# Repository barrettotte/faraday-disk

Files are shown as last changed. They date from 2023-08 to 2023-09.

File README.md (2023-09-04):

# faraday-disk

A Faraday disk built to learn about electromagnetism and early generators.

<a href="images/cad.png">
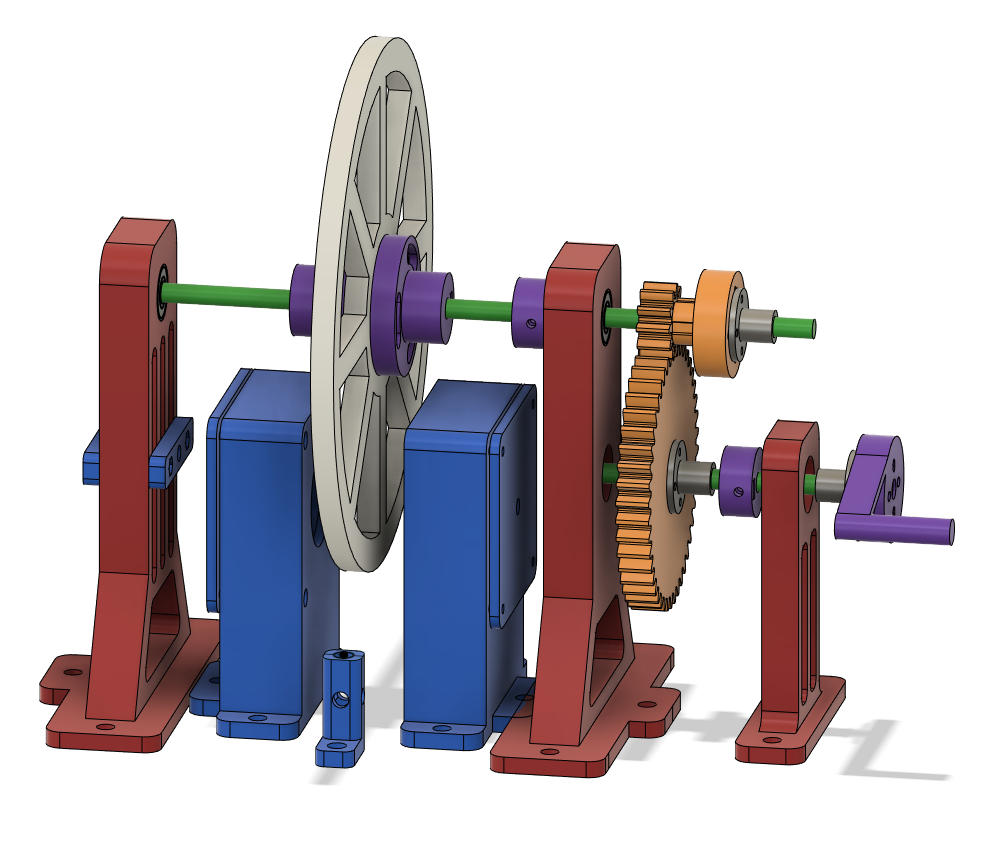
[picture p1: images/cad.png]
cad
  
</a>
<br>
<a href="images/built.jpg">
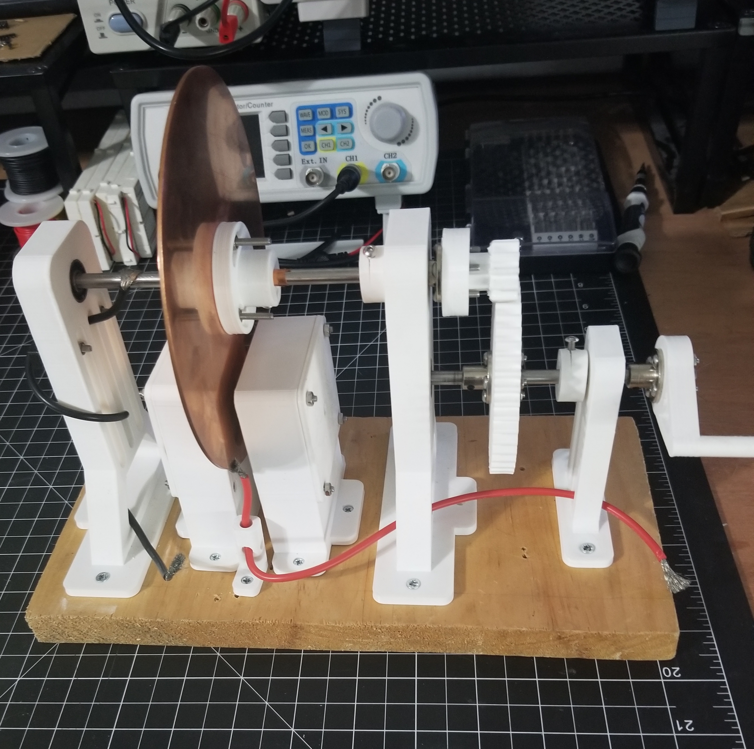
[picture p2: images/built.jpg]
built
  
</a>

Write up with some concepts, equations, and math is located in [faraday-disk.md](faraday-disk.md)

## Performance

At around 200rpm, the generator produces voltage of around 1.9-2.1mV and current of 0.1μA.
Theoretically (no losses), with this design I should have gotten 0.18V and 0.8007A.

As expected, this generator performed far from ideally.

I think most of the loss comes from brush contacts, oxidation on the copper disk,
and the effects of eddy currents.

## Parts List

- 6mm (606) bearings (x4)
- 6mm axle, ~120mm
- 6mm axle, ~180mm
- Stranded wire for brushes
- 40x20mm neodymium magnets (x2) ([amazon](https://www.amazon.com/dp/B095SDDZ92))
- Copper foil (for continuity between disk and axle)
- 150mm copper disk ([amazon](https://www.amazon.com/dp/B0BNDM489N))
- 3D printed parts
  - [cad/axle-2-support.stl](cad/axle-2-support.stl)
  - [cad/axle-cap](cad/axle-cap.stl) (x2)
  - [cad/brush-mount-bolt.stl](cad/brush-mount-bolt.stl)
  - [cad/brush-mount-bottom.stl](cad/brush-mount-bottom.stl)
  - [cad/brush-mount-nut.stl](cad/brush-mount-nut.stl)
  - [cad/coupler-bolt.stl](cad/coupler-bolt.stl) (x2)
  - [cad/hand-crank.stl](cad/hand-crank.stl)
  - [cad/magnet-brush-mount-large-lid.stl](cad/magnet-brush-mount-large-lid.stl) (x2)
  - [cad/magnet-brush-mount-large.stl](cad/magnet-brush-mount-large.stl)
  - [cad/spur-gear-11.stl](cad/spur-gear-11.stl)
  - [cad/spur-gear-44.stl](cad/spur-gear-44.stl)
  - [cad/stand-left.stl](cad/stand-left.stl)
  - [cad/stand-right.stl](cad/stand-right.stl)
- Various m3 bolts, nuts, and washers (lost track while building and redesigning...I'm dumb)

## References

- https://en.wikipedia.org/wiki/Homopolar_generator
- [An Introduction to Classical Electrodynamics by Keohane; Foy](https://isbnsearch.org/isbn/9781949942002)
- [University Physics with Modern Physics (14th Edition) by Young, Hugh D.; Freedman, Roger A.](https://isbnsearch.org/isbn/9780321973610)
- [The Homopolar Handbook by Valone, Thomas](https://isbnsearch.org/isbn/9780964107014)
- [The Unipolar Generator: A Demonstration of Special Relativity, Berg; Alley](references/unipolar-generator-special-relativity-berg-alley.pdf)
- https://en.wikipedia.org/wiki/Classical_electromagnetism_and_special_relativity
- [Unipolar Induction A Messy Corner of Electromagnetism, Härtel](references/unipolar-induction-messy.pdf)
- [Notes on a Unipolar Dynamo, Tesla (1891)](references/unipolar-dynamo-tesla.pdf)
- [Untried Homopolar Generator Experiments, Beaty](http://amasci.com/freenrg/n-mach.html)
- https://en.wikipedia.org/wiki/Faraday_paradox
- https://en.wikipedia.org/wiki/Eddy_current
- [The Feynman Lectures on Physics, Volume II, Lecture 17](https://www.feynmanlectures.caltech.edu/II_17.html)

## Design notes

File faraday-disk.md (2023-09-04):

# Faraday Disk

## Introduction

A bit of a disclaimer, I barely know any physics. 
So, I probably got some terminology or calculations wrong.
This project was completed to learn more about electromagnetism.

The Faraday disk is an electrical generator that produces low voltage and high current.
It is unique since it is the only generator that produces true direct current without the need of rectifiers or commutators. But, it should be noted that the original design is an extremely inefficient generator.
The Faraday disk was first developed by Michael Faraday in 1831 during a series of experiments involving induction.

Searching around the internet for "Faraday disk" and "homopolar generator" will lead you to some strange pages on aether, free energy, and over unity. 
Without going into detail on some of the absurdity, I'm just going to say that I side with the beliefs of the last 100 years of physics and these three topics can be ignored.

## Physics

### Faraday's Law of Induction

In a Faraday disk, the magnetic field is static and the conductor is moved, this produces motional EMF.
The conductor is "cutting field lines" to induce EMF and current.

Faraday's Law of induction:

$$\epsilon=-\frac{d\Phi_B}{dt}$$
where
- $\epsilon$ is the induced electromotive force
- $\Phi_B$ is the magnetic flux

This direction (negative sign) is determined by Lenz's law.
Lenz's law states that the direction of induced EMF is such as to oppose the very cause producing it.

It turns out that Faraday's law is invalid for use with calculating induced EMF for the Faraday disk.
Instead, we need to use a derivation of the Maxwell-Faraday equation to determine motional EMF.

### Lorentz Force

The Lorentz force is used to describe the force experienced by a charged particle when moving through an electromagnetic field.
This can be calculated with the following formula:

$$\vec{F} = q(\vec{E} + \vec{v}\times \vec{B})$$
where
- $q$ is the charge of the particle
- $\vec{E}$ is the external electric field
- $\vec{v}$ is the velocity of the particle
- $\vec{B}$ is the external magnetic field

The charge of an electron is equal to $-1.602\times10^{-19}\text{ coulombs}$.

The Lorentz force is responsible for the generation of electrical current in the Faraday disk.
This in turn produces electromagnetic forces within the disk that produces a counter or back torque that opposes rotation.

### Maxwell-Faraday Equation

The Maxwell-Faraday equation is used to generalize Faraday's law and it solves the problem
mentioned earlier when Faraday's law fails during motional EMF of the Faraday disk.

$$\nabla\times\vec{E}=-\frac{\partial{\vec{B}}}{\partial t}$$
where
- $\vec{E}$ is the electric field
- $\vec{B}$ is the magnetic field
- $\nabla\times$ is the curl operator

<br>

Or in the integral form using Kelvin-Stokes theorem:

$$\oint_C\vec{E}\cdot\vec{dl} = -\frac{d}{dt}\iint_S \vec{B}\cdot\vec{dA}$$
where
- $C$ is a closed loop
- $\vec{E}$ is the electric field
- $\vec{dl}$ is the infinitesimal vector element along path of integration $C$
- $S$ is the closed surface bounded by loop $C$
- $\vec{B}$ is the magnetic field
- $\vec{dA}$ is the infinitesimal vector element of area on surface $S$

<br>

The Maxwell-Faraday equation is basically used to describe how changing magnetic fields
induce electric fields and how electric fields circulate around closed loops 
due to the magnetic field changes.

### Induced EMF in Faraday Disk

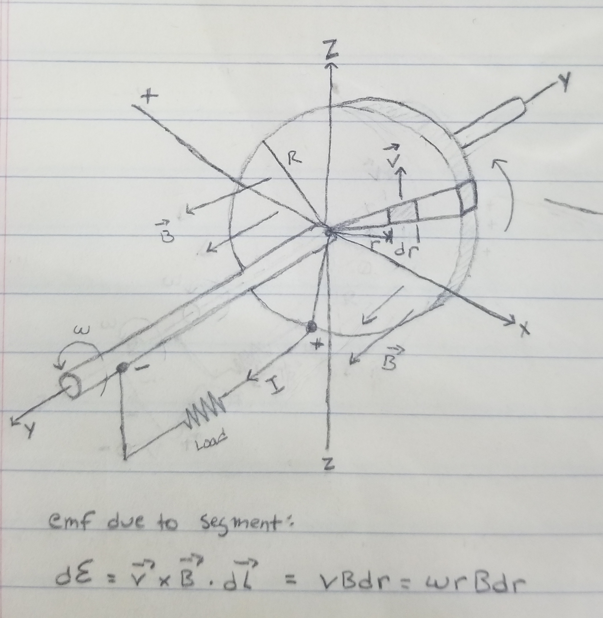
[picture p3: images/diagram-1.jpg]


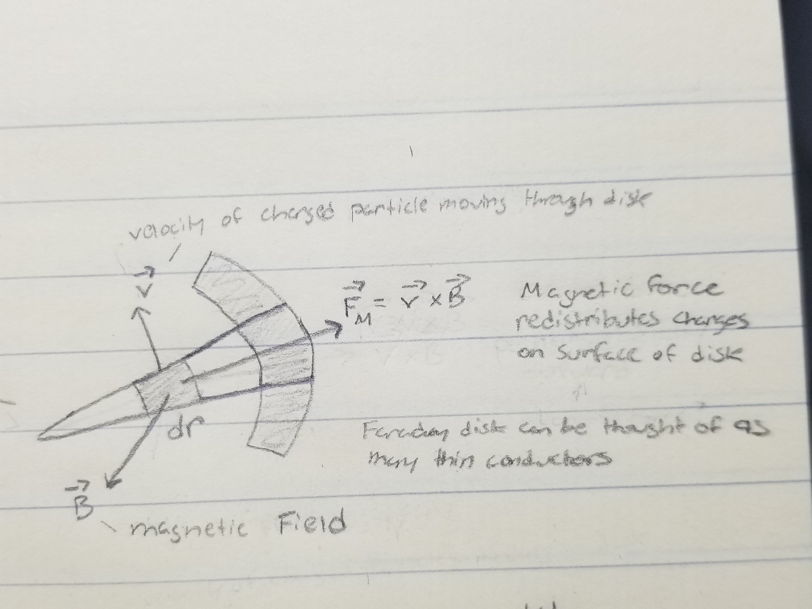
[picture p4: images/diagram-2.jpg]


Given the integral form of Maxwell-Faraday equation,

$$\oint_C\vec{E}\cdot\vec{dl}=-\frac{d}{dt}\iint_S\vec{B}\cdot\vec{dA}$$

Since the Faraday disk is the case of a conductor moving through a magnetic field, 
the equation can be simplified for a general case of motional EMF:

$$\epsilon=\oint_C(\vec{v}\times\vec{B})\cdot\vec{dl}$$

Since we're only interested in the EMF due to the Lorentz force from the center of the disk
to the edge of the disk, the motional EMF equation can be simplified to:

$$\epsilon=\oint_C(\vec{v}\times\vec{B})\cdot\vec{dl}
=\int_0^R(\vec{v}\times\vec{B})\cdot\vec{dl}$$
where
- $\epsilon$ is the induced electromotive force (EMF)
- $C$ is the path of the circuit, between center 0 and rim $R$ of disk
- $\vec{v}$ is the velocity of conductor element
- $\vec{B}$ is the magnetic field at position of conductor element
- $\vec{dl}$ is a small vector element across path of integration on conductor, pointing in direction of path $C$

We integrate from 0 to $R$ since only part of the disk is non-parallel to $\vec{B}$ at a given point in time.

Notice that $\vec{v}\times\vec{B}$ is the magnetic portion of the Lorentz force, since the Faraday disk
is rotating in a static magnetic field.

Given the induced EMF caused by a segment of the disk, $d\epsilon$:

$$d\epsilon = (\vec{v}\times\vec{B})\cdot\vec{dl}=vBdr=\omega rBdr$$
where
- $dr$ is a slice of a radial segment of the disk
- $\omega$ is the angular velocity of the charged particle
- $\omega=vr$
- $r$ is the distance from the center of the disk

The EMF equation above can now be simplified to:

$$\epsilon=\int_0^R(\vec{v}\times\vec{B})\cdot\vec{dl}
=\int_0^R(\omega Br)\ dr
=wB\int_0^Rr\ dr
=wB(\frac{r^2}{2})\ \Big|_0^R
=\frac{1}{2}\omega BR^2$$

### Eddy Currents

In theory the Faraday disk has low potential difference and large current flow. However, the current is not competely radial
due to the static magnetic field not passing the entire surface of the disk. 
This produces Eddy currents that oppose the current produced due to the changing magnetic field.

Eddy currents are circular currents induced in a conductor when it is exposed to a changing magnetic field.

In other words, the magnets are only covering a segment of the disk, 
so the Eddy currents oppose a majority of the current produced directly under the magnets.
If the generator was redesigned to have a static magnetic field across the entire disk, there should be less current loss and less of an opposition to rotation.

The magnitude of an eddy current can be calculated using Faraday's second law of magnetic induction: $$I=-\frac{1}{R}\frac{d\Phi_B}{dt}$$

where
- $R$ is the resistance of the conductor
- $\Phi_B$ is the magnetic flux supplied throughout the conductor

The direction is determined from Lenz's Law or Fleming's right hand rule.
The Lorentz force is responsible for driving the motion of electrons that make up eddy currents.

This is the same concept that is used in electromagnetic braking and why it is so difficult to turn the disk.

### Faraday Paradox

In an alternate configuration of the Faraday disk, often called the "One-piece Faraday generator", the magnet rotates with the disk. 
It seems unintuitive at first, but this still generates voltage even though it seems as though the magnetic field lines are no longer being cut.
Faraday's law seems to predict that this configuration would produce zero EMF, but there is non-zero EMF.
So, the confusion comes from whether or not the magnetic field lines are stationary or rotate.
This is my basic understanding/explanation of the Faraday paradox in relation to the Faraday disk.

The Faraday paradox was reconciled by Einstein's paper on special relativity.
I'm too dumb to understand at the moment, but reading the following may prove helpful:

- [references/unipolar-induction-messy.pdf](references/unipolar-induction-messy.pdf)
- https://en.wikipedia.org/wiki/Moving_magnet_and_conductor_problem
- https://en.wikipedia.org/wiki/Classical_electromagnetism_and_special_relativity

## Actual Performance

Measurements:

- Disk inner radius - 12.7mm
- Disk outer radius - 150mm
- Disk thickness - 1.5mm
- Disk resistance - 0.5 $\Omega$
- Magnetic flux density - 120mT
- RPM - ~200 (counter-clockwise)
- Voltage - ~1.9-2.1mV
- Current - ~0.1 $\mu\text{A}$

RPM was measured by manually counting 50 rotations of hand crank in a minute.
Then, multiplying by gear ratio $50(4)=200$.

## Theoretical Performance

Given
- Disk radius $R=150\text{mm}$
- Magnetic flux density $B=120\text{mT}$
- Angular velocity $\omega=200\text{rpm}$

In SI units:
- $R=150\text{mm}=0.15\text{m}$
- $B=120\text{mT}=0.12\text{T}$
- $\omega=200\text{ rpm} = \frac{200}{60}2\pi=20.94\text{ rad/s}$

Using equation for induced EMF in a Faraday disk:

$$\epsilon=\frac{1}{2}\omega BR^2$$
$$\epsilon=\frac{1}{2}(20.94\text{ rad/s})(0.12\text{ T})(0.15\text{ m})
=0.18\text{ V} = 180\text{ mV}$$

To find theoretical resistance of disk, use equation for resistance of cylindrical conductor
and resistivity of copper $1.724\times 10^{-8}\frac{\Omega}{\text{m}}$

$$R=\frac{\rho L}{A}
=1.724\times 10^{-8}\cdot\frac{0.015}{\pi 0.15^2}
=0.2248\Omega$$
where
- $\rho$ is the resistivity of the material
- $L$ is the length or thickness
- $A$ is the cross-sectional area, $A=\pi R^2$

Using Ohm's Law:

$$I=\frac{V}{R}
=\frac{0.18\text{ V}}{0.2248\Omega}
=0.8007\text{A}$$

## Potential Losses

There's a ton of things that could have went wrong with my design.

- Friction between 3D printed parts, axles, bearings, and brush contacts
- Material resistance of partially oxidized copper
- Lack of conductivity from brush contacts
- Back torque from Lorentz force and eddy currents

## Design

This probably won't be too detailed, but this section will have some notes about why the design is the way it is.

Originally, I planned on 3D printing a disk and wrapping it in a layer of aluminum foil to use as my conducting disk. 
After accidentally punching a hole in three of these disks I decided to buy actual conductive disks.
On Amazon, I managed to find copper and aluminum gem polishing disks to serve as my conductive disk.

The copper disk has an outer diameter of 150mm, inner diameter of 12.7mm, and thickness of 1.5mm. 
The disk was attached to the 6mm steel axle using 3D printed couplers, washers, and copper foil. 
The copper foil and washers were needed to provide continuity between the axle and the larger inner radius of the copper disk. 
This probably lead to unnecessary resistance in the circuit because of this design flaw.

I didn't know what magnets to get, so I found the strongest neodymium magnets easily purchased from Amazon.
These large neodymium magnets are 40x20mm and have roughly a magnetic flux density of 120mT.
The large neodymium magnets were placed as close to the disk as possible without cracking the 3D printed mounts and/or bending too far into the disk.
In hindsight, maybe these magnets were too strong for this design.

To potentially increase angular velocity or RPM, I decided to add a 1:4 gear ratio using 11 and 44 toothed spur gears. 
The basic formula for gear ratios is given by:

$$\frac{\text{driver RPM}}{\text{driven RPM}}
=\frac{\text{teeth driven}}{\text{teeth driver}}
=\frac{11}{44}
=1:4$$

Unfortunately, I believe this made transfer of torque from the hand crank worse.
Combined with the strong opposition from the magnets, it was very difficult to turn the generator and reach high RPM.

The copper disk also has a problem with oxidation. 
At the start of the project, the resistance between the disk and the axle was around $0.1 \Omega$, but over time rose to $0.5 \Omega$ because of the oxidation.
I would have used the aluminum disk, but had a lot of problems getting measureable current, maybe due to the increased thickness.

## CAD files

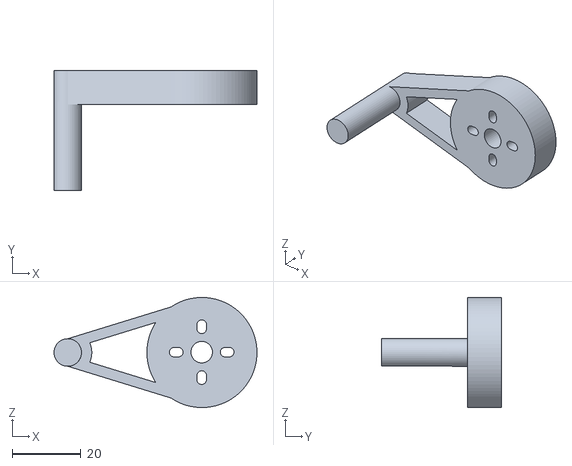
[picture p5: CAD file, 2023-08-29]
cad/hand-crank.stl
59.0 x 35.0 x 32.0

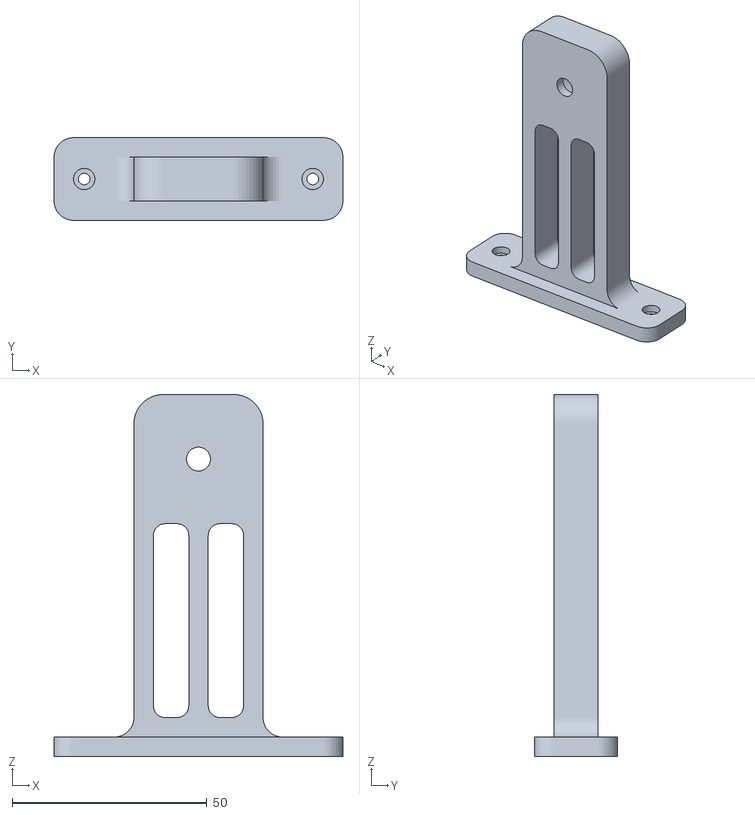
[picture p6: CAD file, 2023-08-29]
cad/axle-2-support.stl
74.1 x 21.2 x 92.9

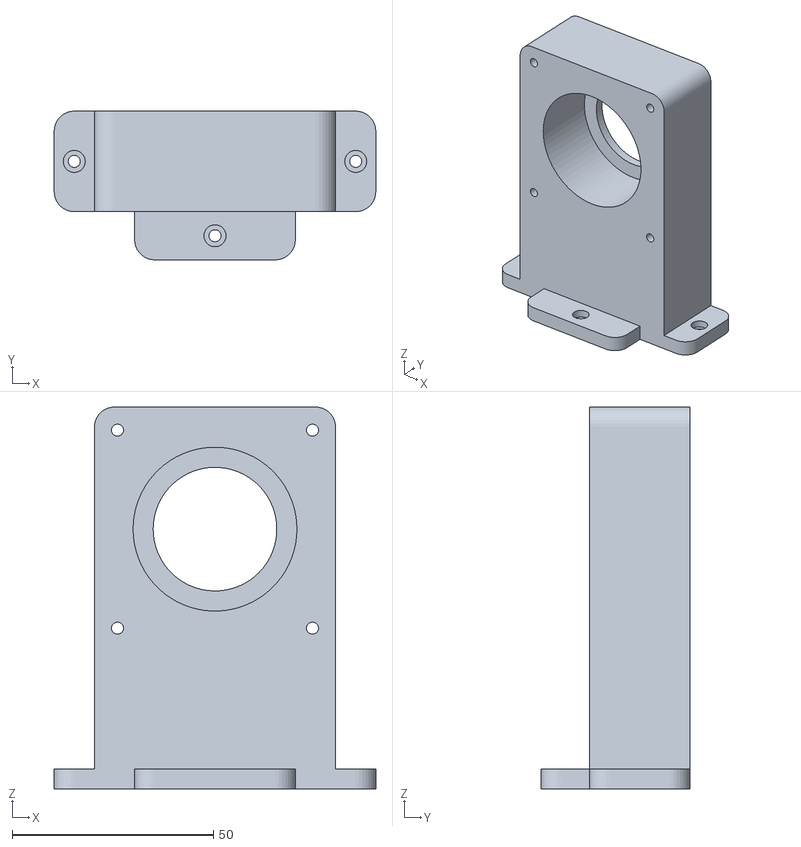
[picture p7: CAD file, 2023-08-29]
cad/magnet-brush-mount-large.stl
80.0 x 37.0 x 95.0

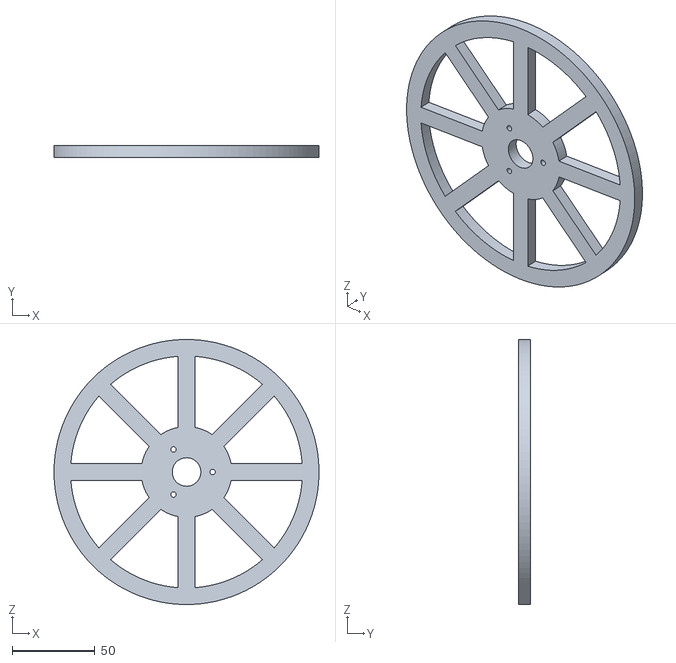
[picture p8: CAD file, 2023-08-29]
cad/disk.stl
160.0 x 7.00 x 160.0

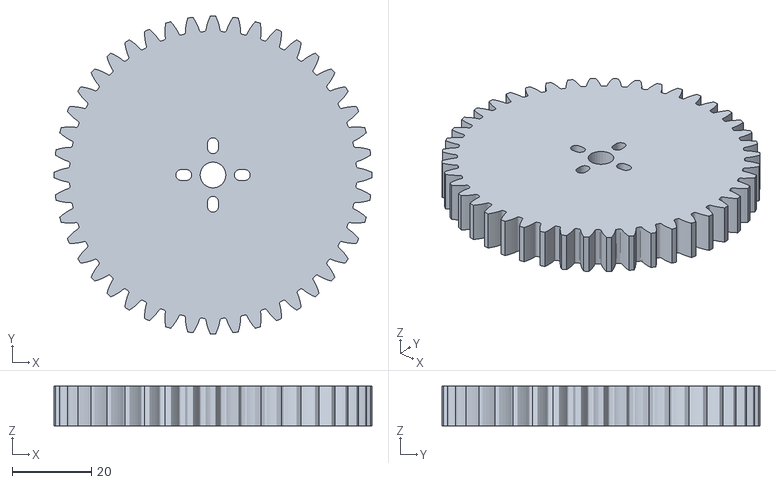
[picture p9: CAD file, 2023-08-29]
cad/spur-gear-44.stl
80.5 x 80.5 x 10.0

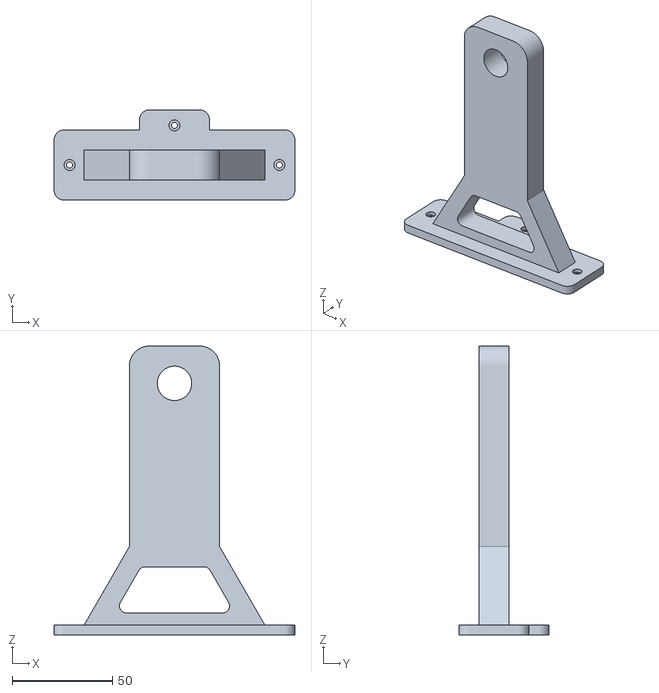
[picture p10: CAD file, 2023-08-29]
cad/stand-right.stl
120.0 x 45.0 x 144.0

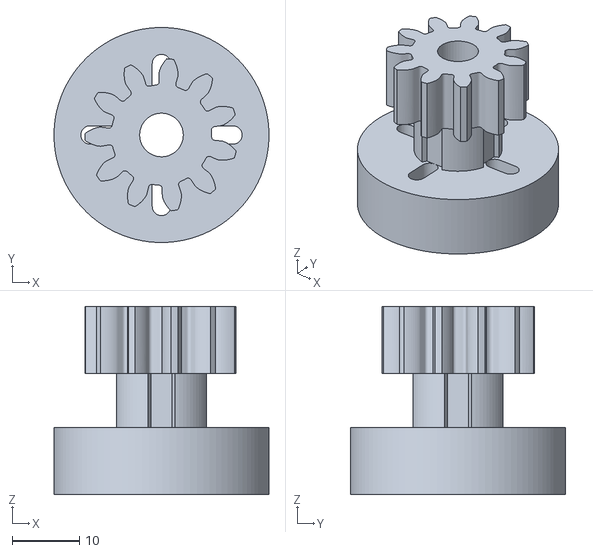
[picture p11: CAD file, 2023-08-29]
cad/spur-gear-11.stl
32.0 x 32.0 x 28.0

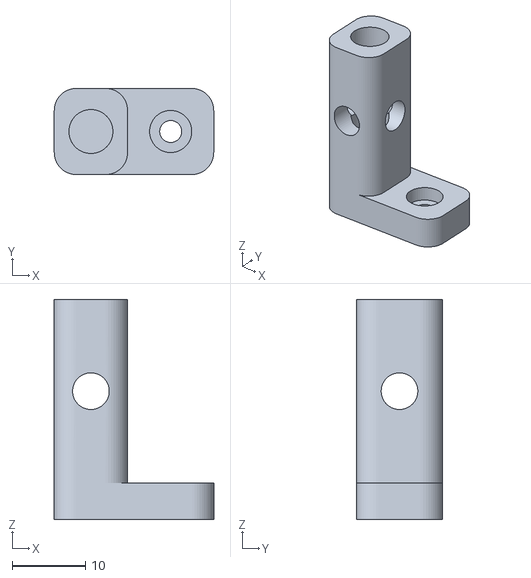
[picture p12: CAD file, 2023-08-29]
cad/brush-mount-bottom.stl
21.8 x 11.8 x 30.0

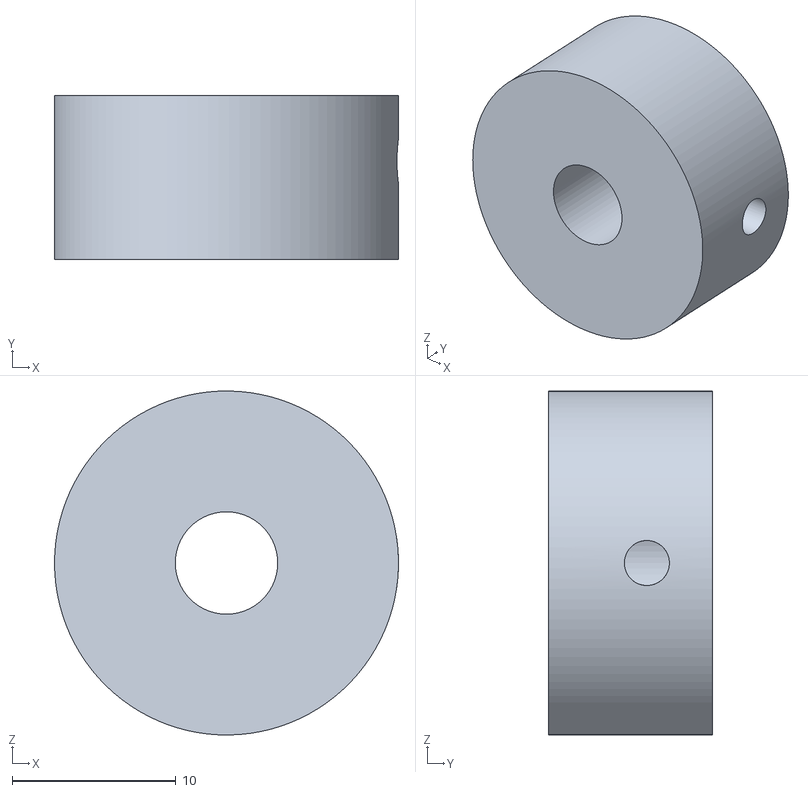
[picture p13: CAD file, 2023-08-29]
cad/axle-cap.stl
21.0 x 10.0 x 21.0

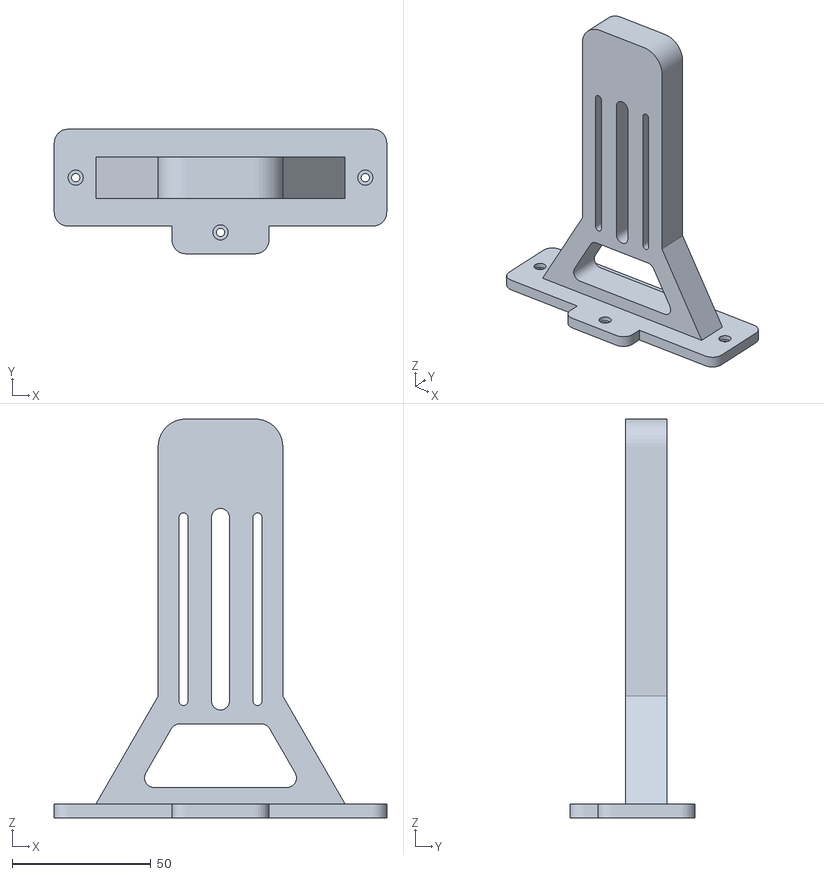
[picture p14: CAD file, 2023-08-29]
cad/stand-left.stl
120.0 x 45.0 x 144.0

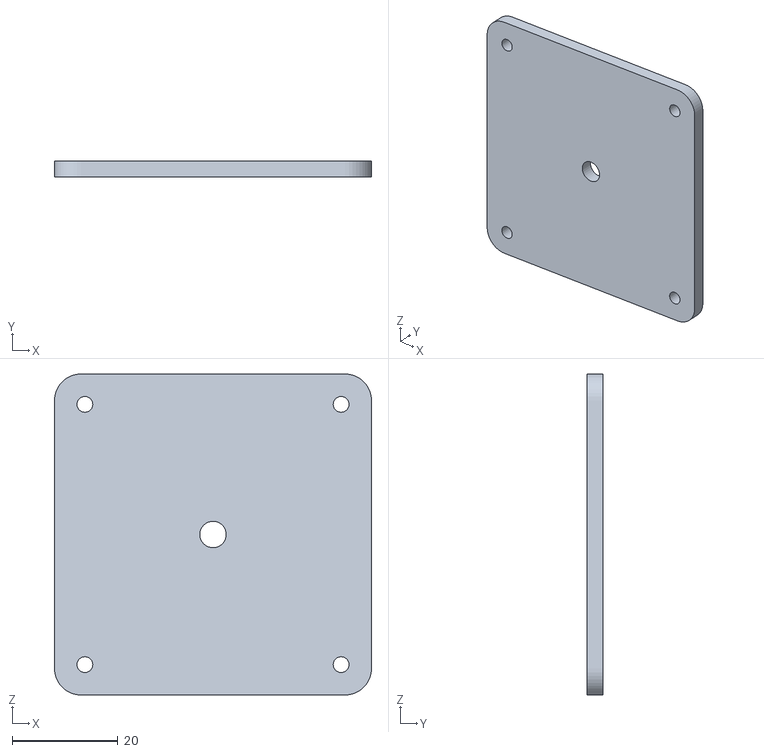
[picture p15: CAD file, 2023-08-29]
cad/magnet-brush-mount-large-lid.stl
60.0 x 3.00 x 60.8

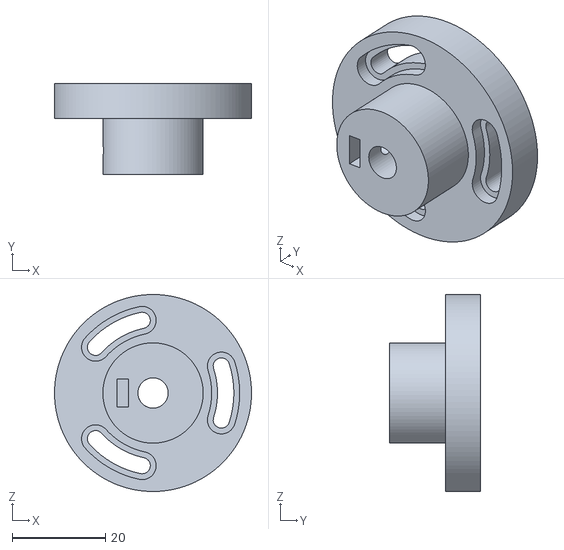
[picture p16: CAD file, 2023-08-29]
cad/coupler-bolt.stl
42.2 x 19.5 x 42.2

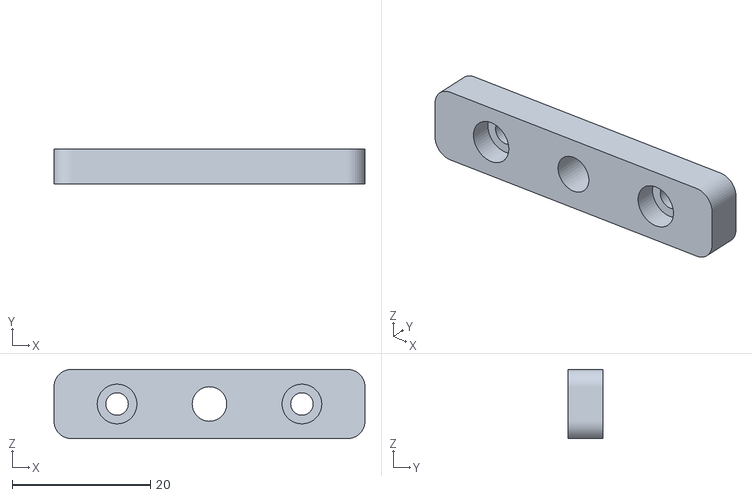
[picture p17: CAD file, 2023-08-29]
cad/brush-mount-bolt.stl
45.0 x 5.00 x 10.0

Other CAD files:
cad/brush-mount-nut.stl
cad/faraday-disk.f3d

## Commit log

2023-07-25 initial cad
    [brush-mount-left.3mf, coupler-bolt.3mf, coupler-nut.3mf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]
2023-07-25 re-export cad as stl
    [brush-mount-left.3mf, brush-mount-left.stl, coupler-bolt.3mf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]
2023-08-29 final cad
    [axle-2-support.stl, axle-cap.stl, brush-mount-bolt.stl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]
